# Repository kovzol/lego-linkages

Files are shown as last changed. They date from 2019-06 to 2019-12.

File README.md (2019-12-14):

# Introduction

This is a collection of simple LEGO linkages that can follow a prescribed motion.
The drawings and assembly instructions are created with the [LEGO Digital Designer (LDD)](https://www.lego.com/en-us/ldd) 4.3,
a free application for Windows and Mac. (Linux users may want to use [CrossOver](https://www.codeweavers.com/products/crossover-linux)
to run LDD with emulation.) After installing LDD, in case you have problems with the Hinge tools,
consider checking [this page](https://steamcommunity.com/sharedfiles/filedetails/?id=455735233).

The linkages are built from a minimal set of LEGO parts. The focus is on the requirement that all
linkages could be built quickly and their movement could be traced on a piece of
paper. See *author's presentation* with title [Teaching algebra and geometry with LEGO and linkages](https://www.researchgate.net/publication/332303931_Teaching_algebra_and_geometry_with_LEGO_and_linkages)
on further details on the topic. Also, an [arXiv paper](https://arxiv.org/abs/1909.04964) is available on using these
linkages in a maths camp.

In LDD one will want to set *View* > *New themes* > *LDD Extended* to make it possible to use
a much wider set of colors for each part.

## The linkages

In all models there is a long red
beam with 15 holes (actually its practicable size is just 14 units) which will be
used to firmly hold the model with the one hand (for right-handed persons this
is the left hand), and a G2 type pen refill which will be inserted in a certain connector
peg, and held and moved with the other hand, on a sheet of paper. This sheet of
paper will be pressed down by the whole construction, practically by the force
of the one hand.

In some linkages an A2 type refill should be used. It ensures a longer distance between
the sheet of paper and the beam than the G2 type, but assembling the linkage should be performed more carefully.
In such cases it may be useful to insert the refill first in the connector peg as deeply as possible,
and only then put the peg in the beam. This has to be done in some cases downside-up, in particular
in the [Parallelograms](#parallelograms). For the other ones an upside-down insertion should work.
Note that A2 type refills can provide a certain backlash in their vertical motion. Make sure you get familiar with their use
before presenting a linkage that is based on A2. Otherwise the drawings could be quite inaccurate.

Before buying the refills you need to note that some G2 type refills are longer than expected and do not ensure an accurate motion.
Some A3 type refills are sometimes sold as A2 type, so be careful when ordering a higher amount of
refills. A3 type refills can also be used but they require more careful calibration of their
vertical position, so A2 refills are always preferred. In a doubt you can try the following products:

* G2: [Kugelschreiberminen Kyome](https://www.plate.de/p/kugelschreiberminen-kyome_45244.html)
* A2: [Schneider Office 575M ISO 12757-2](https://www.myuberpens.com/new-schneider-575-75-office-black-ballpoint-pen-metal-slim-refill-iso-12757-2-a2-made-in-germany-fits-most-vintage-pens.html)

Some linkages contain one or more 1x1 beams that was recently introduced by LEGO
and may be missing from most basic sets. These parts are not absolutely required, but using
them makes the linkage more stable.

### Compass

The simplest linkage is a compass. It produces a regular circular curve.

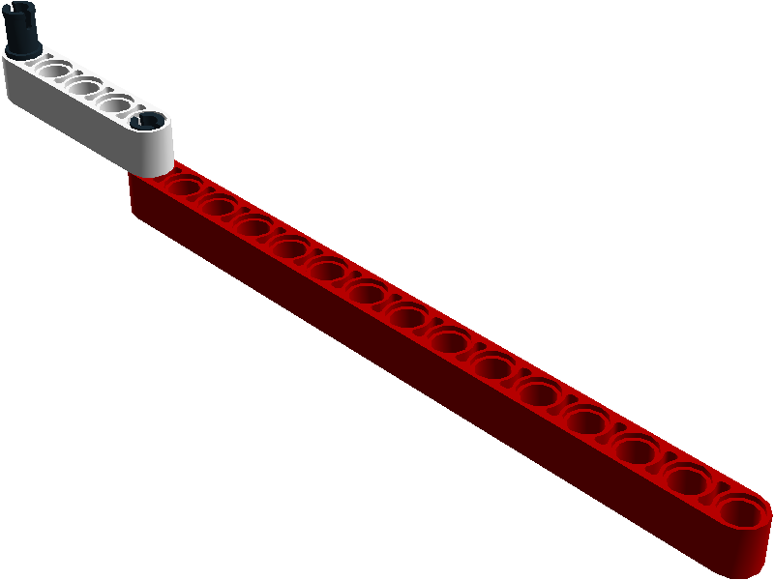
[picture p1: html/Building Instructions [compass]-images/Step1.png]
compass


[Building Instructions](http://htmlpreview.github.io/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).

### Watt's linkage

It is somewhat more difficult... a straight motion to produce. Watt's linkage is an attempt to do that,
with an almost success.

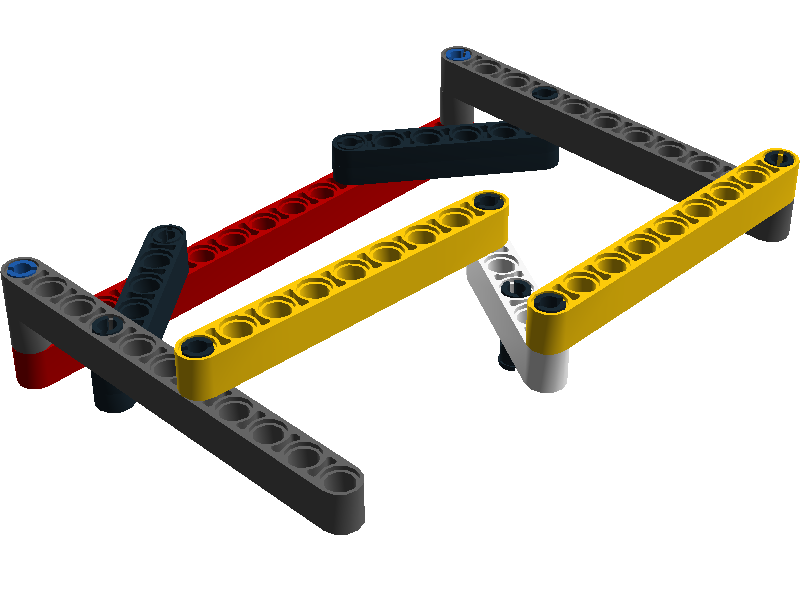
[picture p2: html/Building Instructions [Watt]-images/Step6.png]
Watt's linkage


[Building Instructions](http://htmlpreview.github.io/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).

### Parallelograms

Parallelograms can give a better understanding on the algebraic properties of the movements. Use the A2 refill to draw with them.

#### 8-5

A circle and a lemniscate will be produced, the latter occurs when the parallelogram turns into an anti-parallelogram.

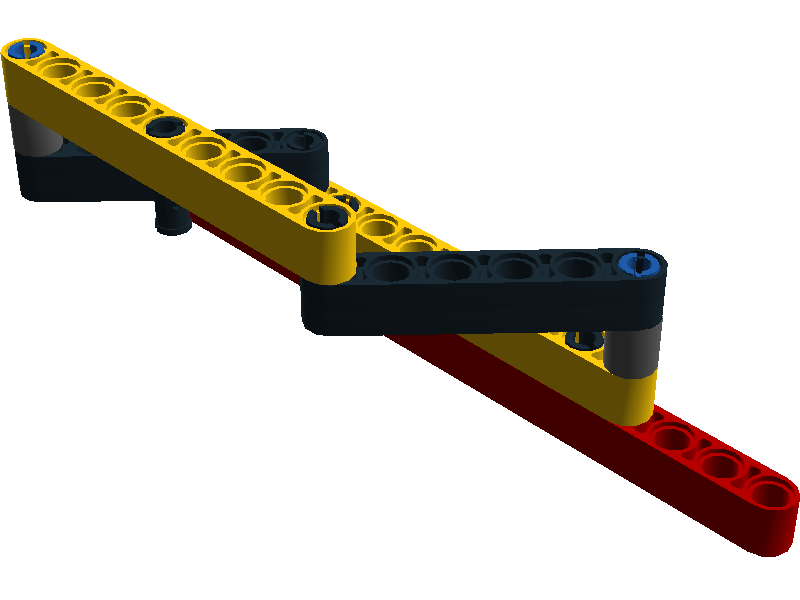
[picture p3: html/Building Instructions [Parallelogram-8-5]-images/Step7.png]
Parallelogram-8-5


[Building Instructions](http://htmlpreview.github.io/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).

#### 4-8

A circle and an almost-circle (a Cassini-oval) will be produced, the latter occurs when the parallelogram turns into an anti-parallelogram.

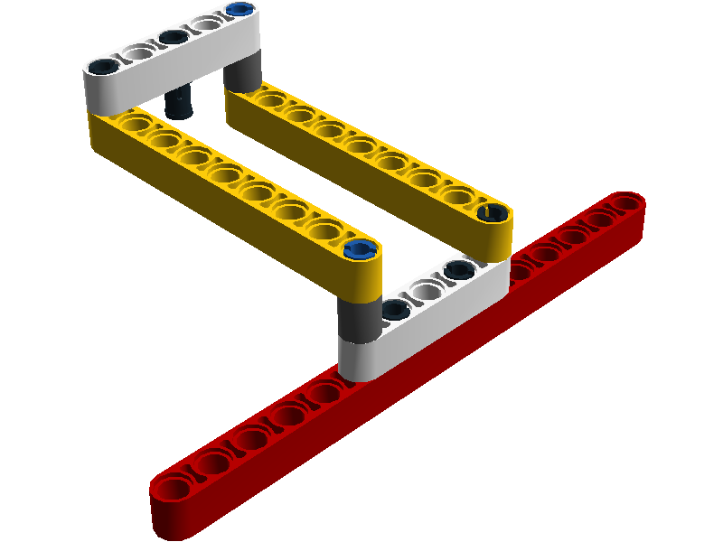
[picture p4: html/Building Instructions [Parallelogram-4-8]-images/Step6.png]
Parallelogram-4-8


[Building Instructions](http://htmlpreview.github.io/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).
This linkage will automatically turn into an anti-parallelogram when the pen refill reaches a critical point.

#### Rhombus

Three circles will be produced. This linkage is actually just a sketch, so the pen refill cannot be used to draw anything.

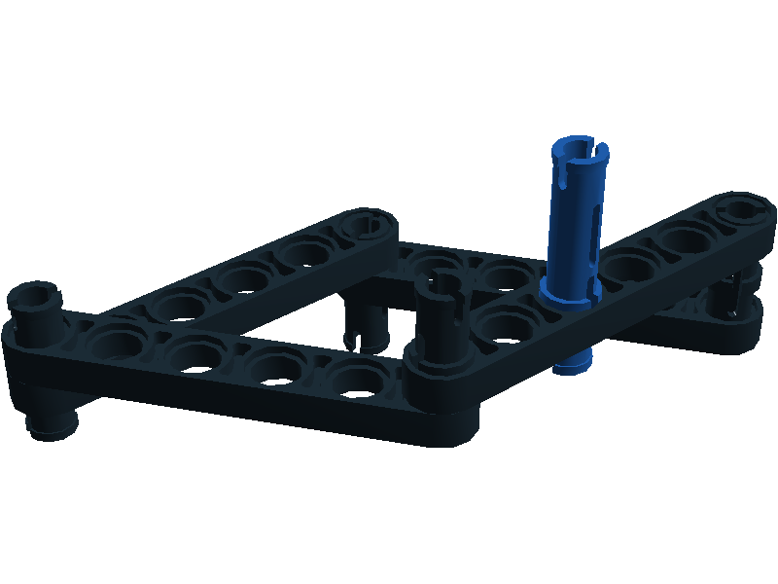
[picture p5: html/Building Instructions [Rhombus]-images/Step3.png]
Rhombus


[Building Instructions](http://htmlpreview.github.io/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).

### Chebyshev's linkage

This is a kind of generalization of the parallelograms (similarly to Watt's linkage). Use a G2 refill.

#### First approach

Chebyshev's linkage seems to produce a circular arc.

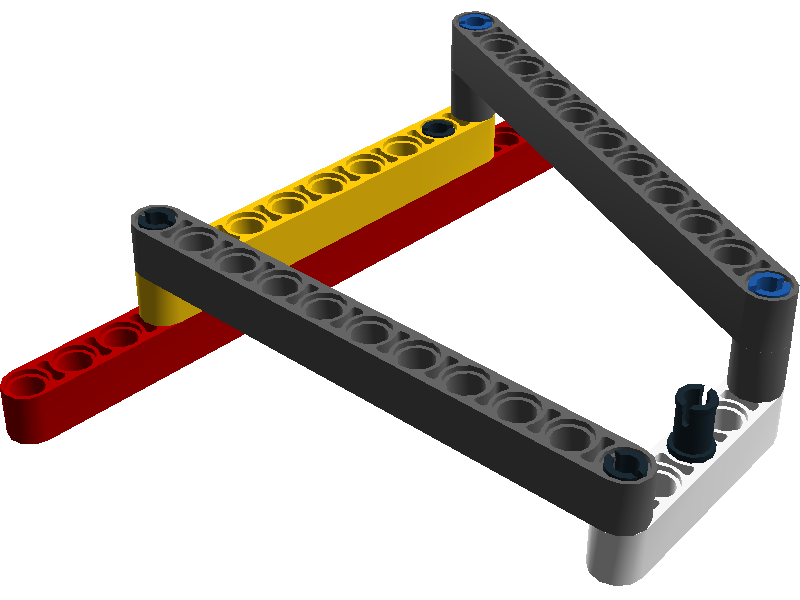
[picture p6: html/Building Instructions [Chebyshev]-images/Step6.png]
Chebyshev's linkage


[Building Instructions](http://htmlpreview.github.io/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).

When its grey bars are crossed, the linkage seems to produce a linear motion.

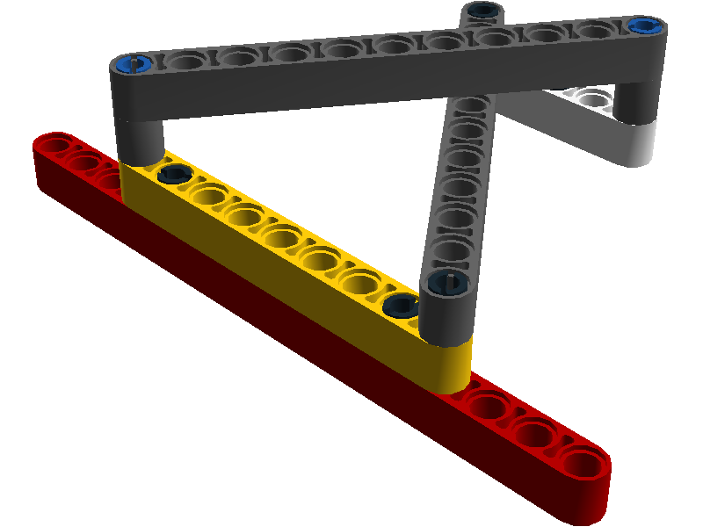
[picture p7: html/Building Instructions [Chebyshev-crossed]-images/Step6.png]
Chebyshev's linkage, crossed bars


#### Second approach

Chebyshev's lambda linkage is equivalent to the previous one, but it can create its path
in one movement as well.

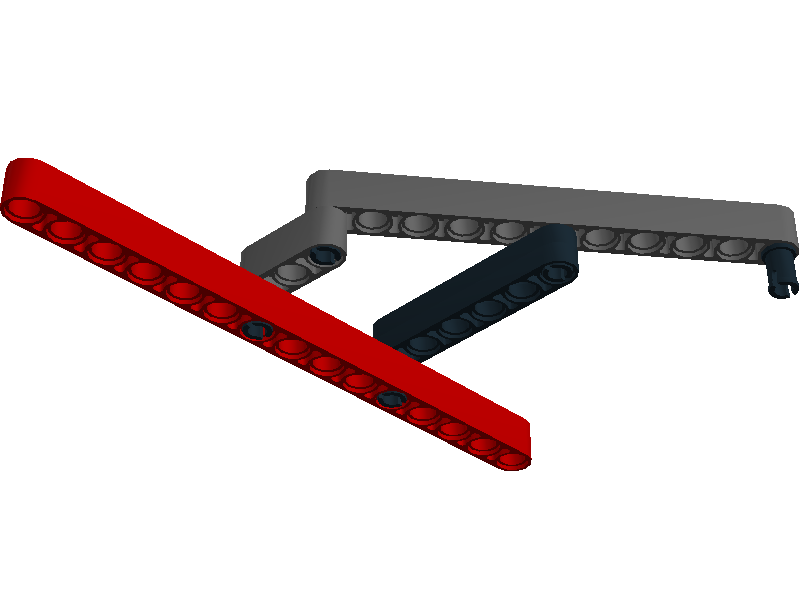
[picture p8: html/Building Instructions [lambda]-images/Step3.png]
Chebyshev's lambda linkage


[Building Instructions](http://htmlpreview.github.io/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).

### Peaucellier's linkage

#### First approach

Peaucellier's linkage provides a linear motion when putting a pen refill in the top-right position.

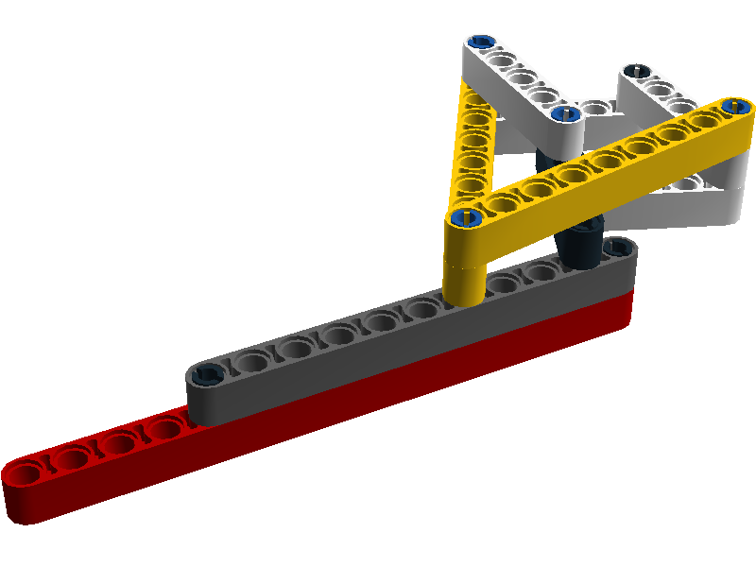
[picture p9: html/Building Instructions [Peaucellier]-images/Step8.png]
Peaucellier's linkage


See also [Building Instructions](http://htmlpreview.github.io/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).
A [GeoGebra applet](https://www.geogebra.org/m/dhpbsjdB) is also available that can be changed a little bit
to get exactly the same motion: *l<sub>1</sub>* has to be set to 8 and *l<sub>2</sub>* to 4 units. Then,
by showing the output labelled with *a* we learn that radius of the circle needs to be 3 units.

Unfortunately there exists no LEGO beam with 3 units (that is, with 4 holes), so we need to use a bigger one.
Here a 4 units long beam is used (with 5 holes). The standard kit (explained in the author's presentation
on page 93 in the Shopping list slide) has to be extended by two blue long pins, one white 5 holes beam
and one black 5 holes beam.

Alternatively a 3 units long beam with 4 holes could be printed with a 3D printer instead of the black 5 holes beam,
see [Andreas Kiener](https://www.uni-salzburg.at/index.php?id=205610)'s [contribution](3d-printing/technic-4m.openjscad.txt) as an
[OpenJSCAD](https://openjscad.org/) file.
In addition, instead of the 11-long beam two halves of 6-long beams may also be used (see a
[photo](3d-printing/Peaucellier.jpg)).

#### Second approach

If we omit a possible requirement that the ball pen point needs to intersect the line of the red beam in the same
distance as the two long beams are, then we can build a Peaucellier-type linkage with the standard set as well.
In this case we need only an extra long pin that is a minimal extra cost and no 3D printing is required.
Another benefit is that the drawn line is quite long (about 12 cm). This linkage requires an A2 type refill.

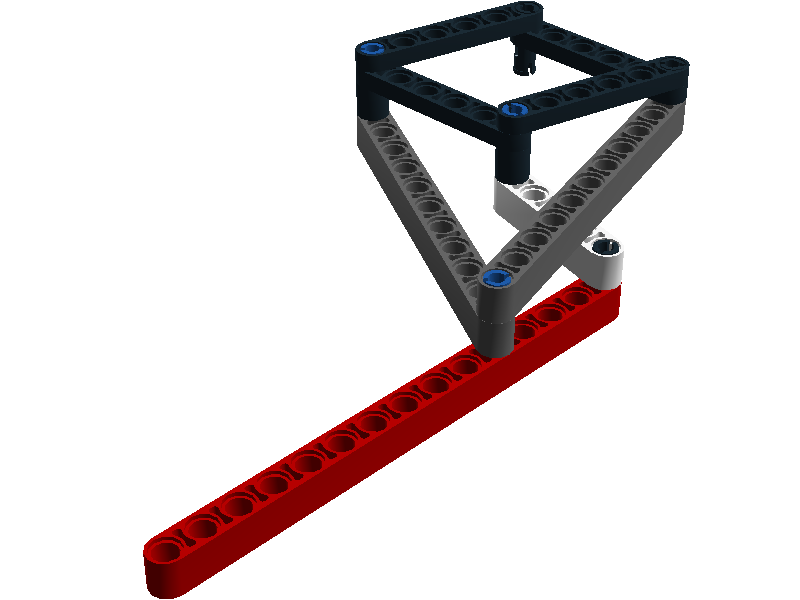
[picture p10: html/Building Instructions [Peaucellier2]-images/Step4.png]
Peaucellier's linkage, second approach


See also [Building Instructions](http://htmlpreview.github.io/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).

### Incomplete linkage as a puzzle

Students may want to solve a puzzle by completing Peaucellier's cell to complete it to the linkage that
produces a straight line. This construction is same as the previous but we just omitted the white constraint.

See the [Building Instructions](http://htmlpreview.github.io/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).

### Hart's A-frame

Another linear motion that requires an A2 pen refill. It is the same linkage that is shown in the author's
presentation on page 88 and [was announced in his blog](https://kovz0l.blogspot.com/2018/08/harts-frame-revisited.html).
There is one minor modification, however. There are two 1x1 parts used to get the linkage more fixed,
according to Andreas' idea.

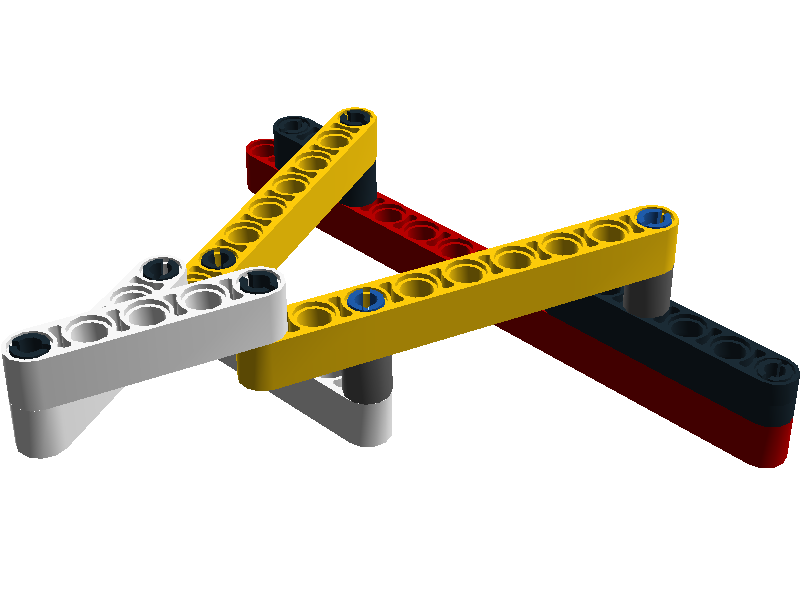
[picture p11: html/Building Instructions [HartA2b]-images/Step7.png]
Hart's A-frame


A big advantage of an earlier version of this linkage is that a much longer straight line can be drawn with it.
Another possibility is to use
the black 5 holes beam from the extended set (see Peaucellier's linkage above) instead of the two half 6 holes beam.

Here are the [Building Instructions](http://htmlpreview.github.io/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).

### Hart's inversor

Another element of the kit that produces a linear motion (again, with a G2 pen refill).

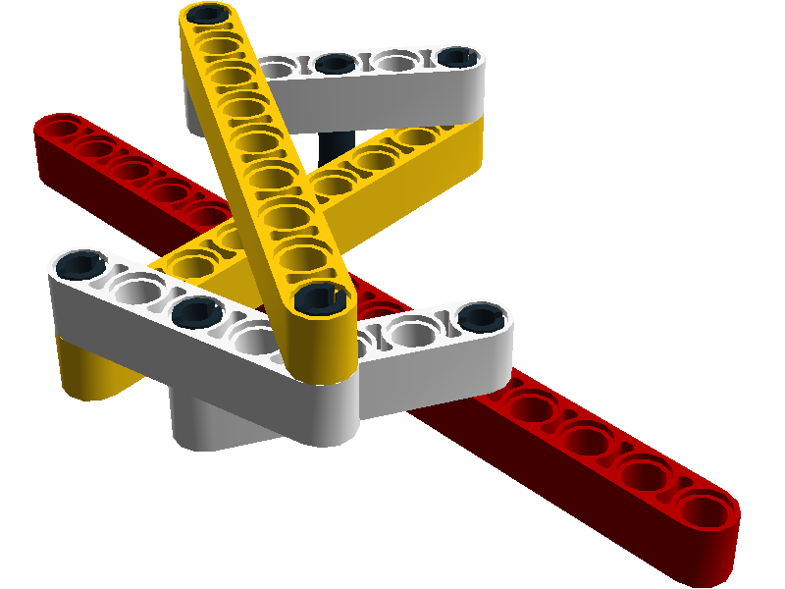
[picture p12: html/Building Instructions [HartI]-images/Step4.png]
Hart's inversor


[Building Instructions](http://htmlpreview.github.io/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).

## Suggested LEGO set to use

Author's presentation suggests the *standard set* (version 2 in the table below). To build the second approach of the Peaucellier cell, one
also needs to have another long pin. Two 1x1 parts can be very useful to minimize vertical movement of the linkage,
that is, to take up the slack. Here is an up-to-date list of the parts of the suggested LEGO set:

| Ver&shy;sion | Date | Beam 15 red 32278 | Beam 11 gray 32525 | Beam 9 yel&shy;low 40490 | Half beam 6 gray 32063 | Beam 5 white 32316 | Beam 3 gray 32523 | Beam 1x1 gray 18654 | Long pin blue 6558 | Pin black 2780 | G2 re&shy;fill | A2 re&shy;fill | 
|:---:|:---:|:---:|:---:|:---:|:---:|:---:|:---:|:---:|:---:|:---:|:---:|:---:|
| 1 | Dec 2017 | 1 | 2 | 2 | 4 | 3 | 1 | - | 2 | 9 | 1 | - |
| 2 | Feb 2019 | 1 | 2 | 2 | 4 | 3 | 1 | - | 2 | 9 | 1 | 1 |
| 3 | Jun 2019 | 1 | 2 | 2 | 4 | 3 | 1 | 2 | 3 | 9 | 1 | 1 |

## Used pen refills in the linkages
| Linkage | G2 | A2 |
|:---:|:--:|:--:|
| compass | x  | |
| Watt | x  | |
| Parallelogram-8-5 | | x  |
| Parallelogram-4-8 | | x  |
| Chebyshev | x  | |
| lambda | x  | |
| Peaucellier | x  | |
| Peaucellier2 | | x  |
| P-cell | | x  |
| HartA2b | | x  |
| HartI | x  | |

# Acknowledgements

* Tomás Recio (for the idea)
* Benedek Kovács (for constructing some of the linkages in LDD)
* Alex Mittermayr (for several ideas on the method how the linkages should be built)
* Andreas Kiener (for minor improvement ideas)
* Chris Sangwin (for several mathematical ideas and concepts from his book [How round is your circle?](https://press.princeton.edu/titles/8624.html))

Many thanks for additional support to:
* Georg Grasegger
* Markus Hohenwarter
* Barbara Lichtenegger
* M. Pilar Vélez
* Susanne Thrainer

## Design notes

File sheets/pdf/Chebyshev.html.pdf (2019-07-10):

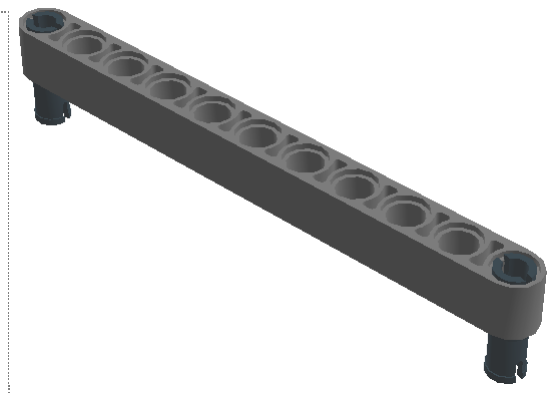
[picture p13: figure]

1 x

2 x

Step 1 of 6

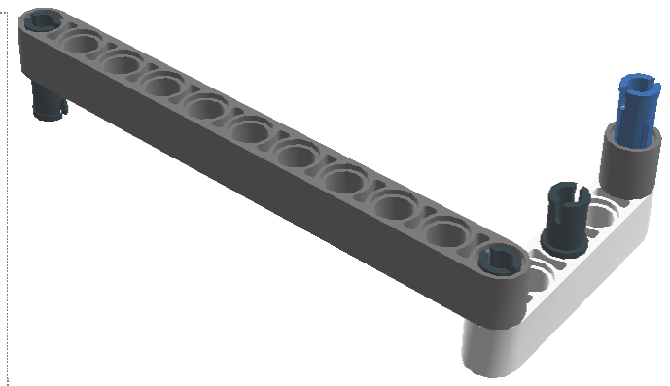
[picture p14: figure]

1 x

1 x

1 x

1 x

Step 2 of 6

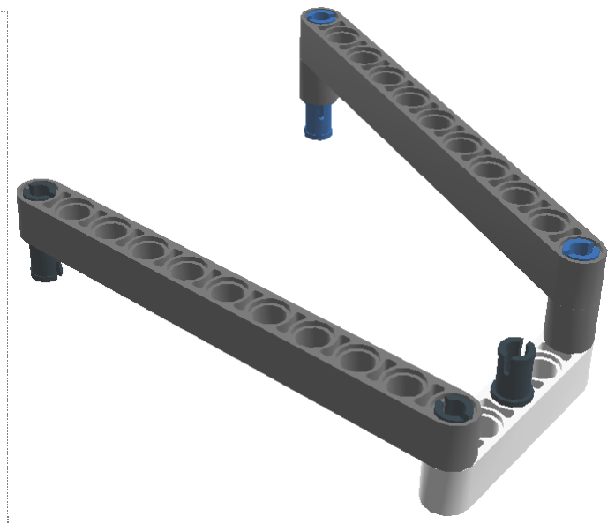
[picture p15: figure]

1 x

1 x

1 x

Step 3 of 6

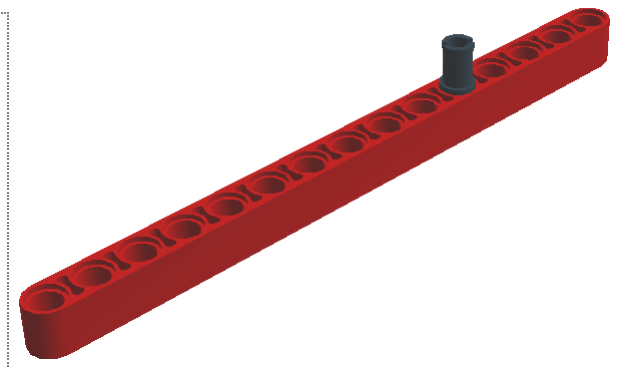
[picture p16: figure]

1 x

1 x

Step 4 of 6
Step 5 of 6

# Chebyshev

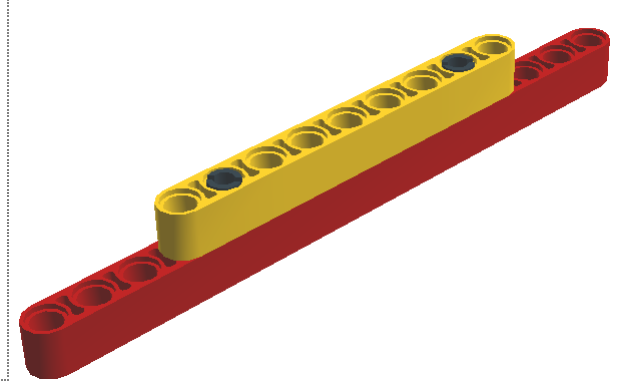
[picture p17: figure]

1 x

1 x

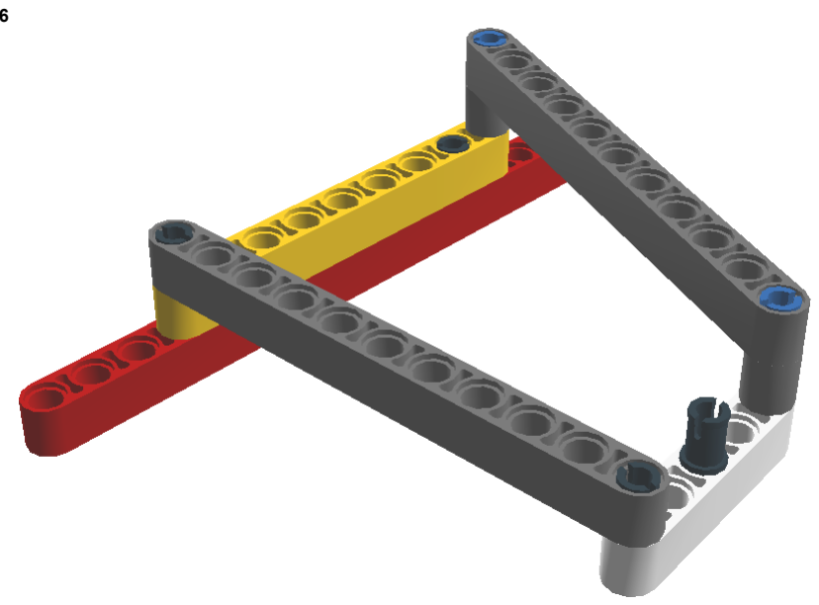
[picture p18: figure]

Step 6 of 6

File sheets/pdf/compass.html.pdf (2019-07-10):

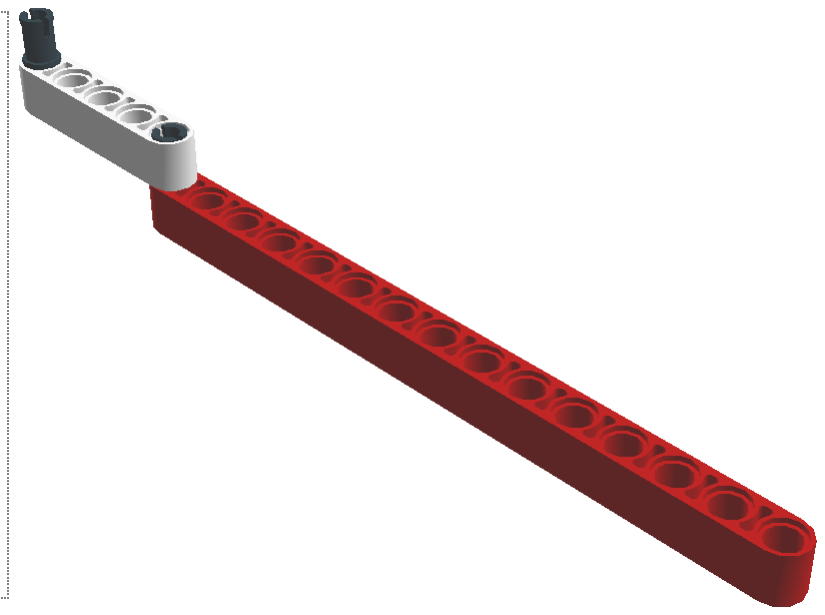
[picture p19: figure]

1 x

1 x

2 x

Step 1 of 1

# compass

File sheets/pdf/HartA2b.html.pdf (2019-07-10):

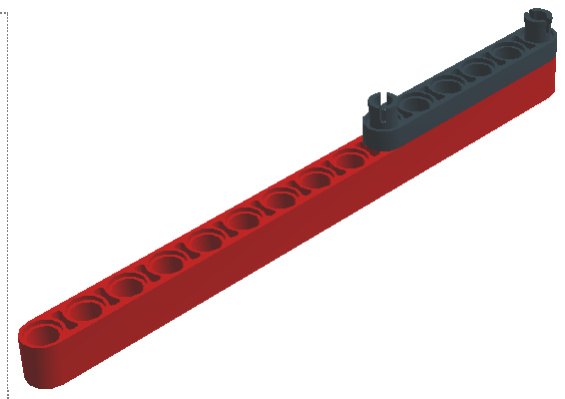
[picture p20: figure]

1 x

1 x

2 x

Step 1 of 7

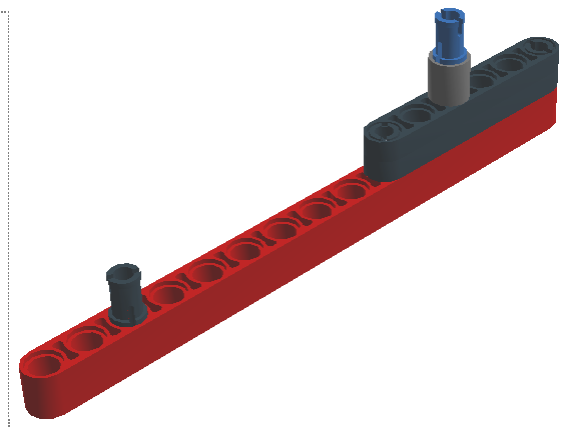
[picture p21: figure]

1 x

1 x

1 x

1 x

Step 2 of 7

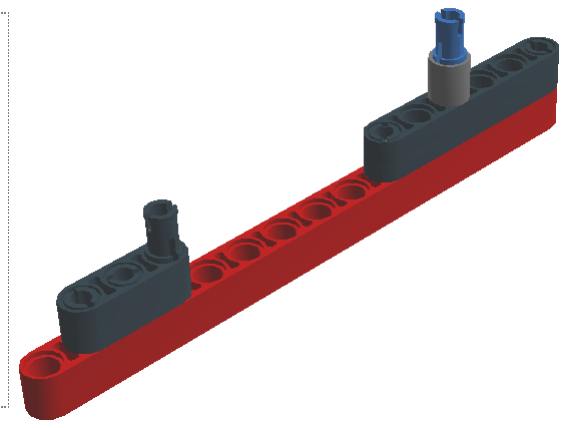
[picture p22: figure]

1 x

2 x

Step 3 of 7

1 x

1 x

Step 4 of 7

# HartA2b

1 x

1 x

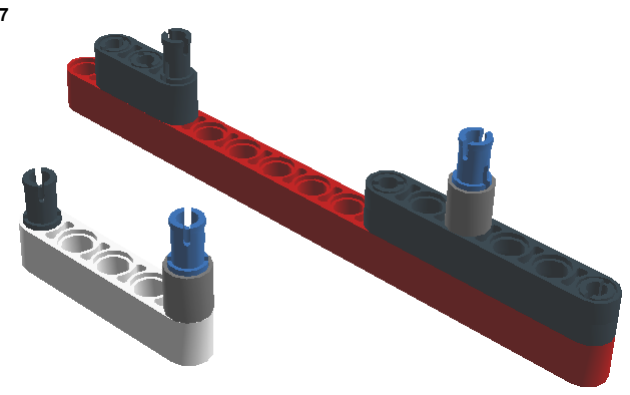
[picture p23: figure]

Step 5 of 7

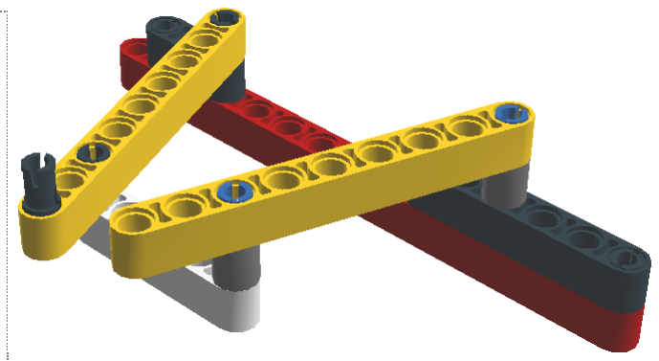
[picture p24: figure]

2 x

1 x

Step 6 of 7

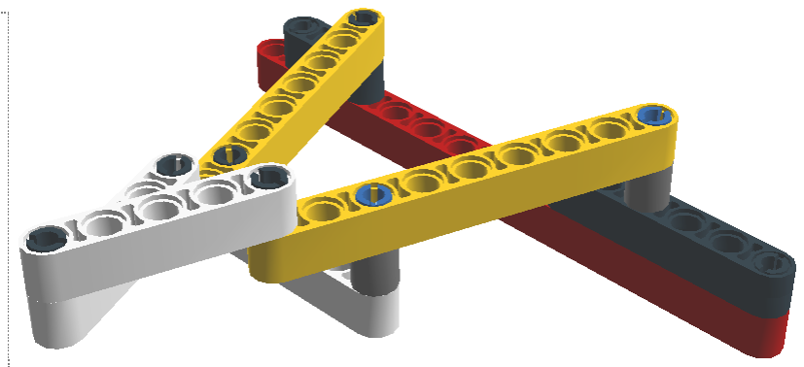
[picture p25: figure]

2 x

1 x

1 x

Step 7 of 7

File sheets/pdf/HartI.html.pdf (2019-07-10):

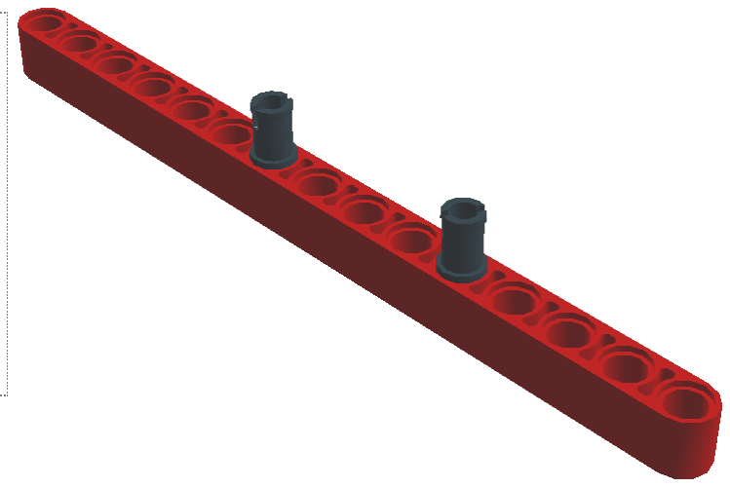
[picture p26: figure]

1 x

2 x

Step 1 of 4

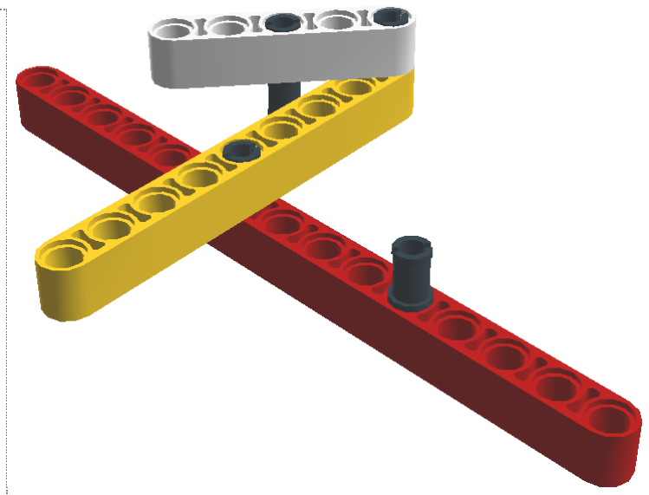
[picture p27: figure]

1 x

1 x

2 x

Step 2 of 4

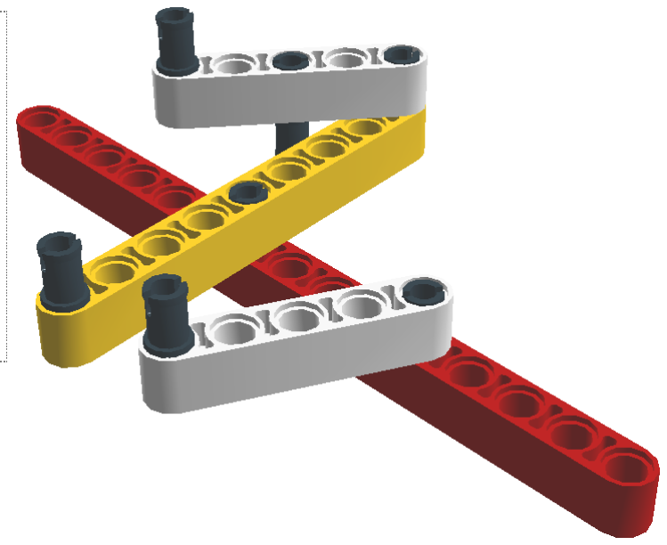
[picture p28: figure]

1 x

3 x

Step 3 of 4

1 x

1 x

1 x

Step 4 of 4

# HartI

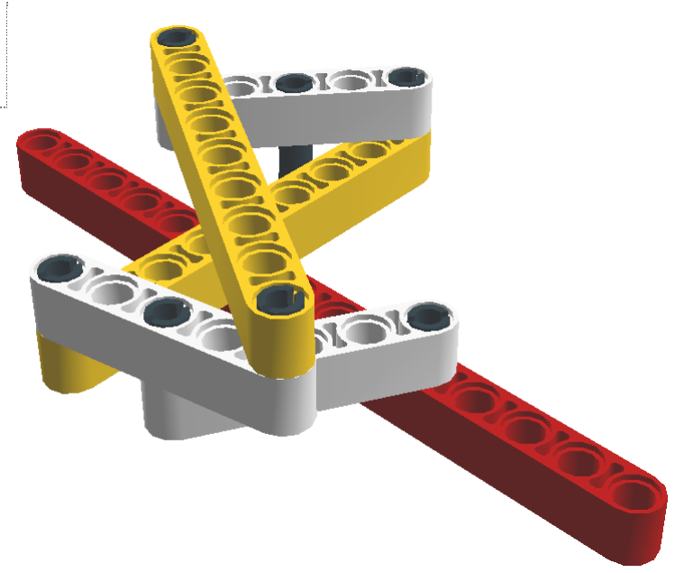
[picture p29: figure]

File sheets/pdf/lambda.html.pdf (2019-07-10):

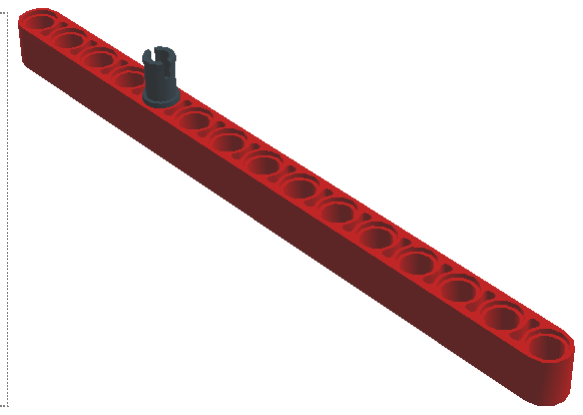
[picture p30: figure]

1 x

1 x

Step 1 of 3

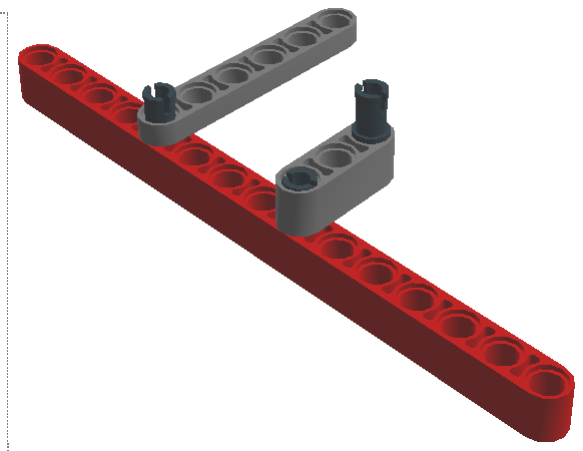
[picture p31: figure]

1 x

1 x

2 x

Step 2 of 3

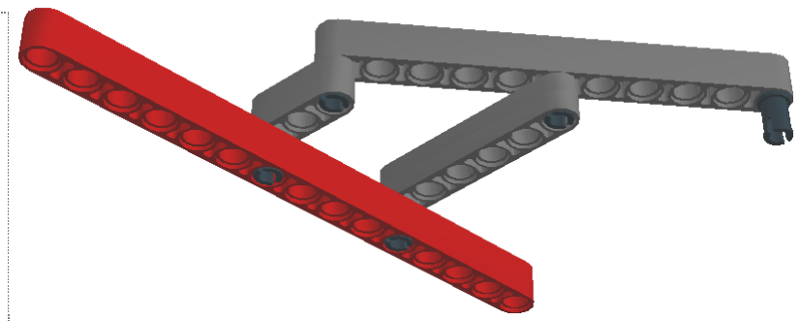
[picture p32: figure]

1 x

1 x

2 x

Step 3 of 3

# lambda

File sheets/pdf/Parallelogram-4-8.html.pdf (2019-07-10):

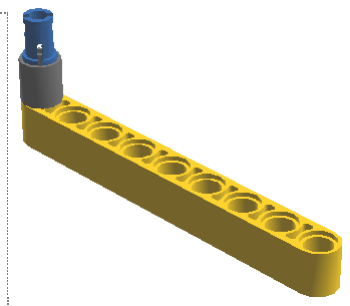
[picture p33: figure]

1 x

1 x

1 x

Step 1 of 6

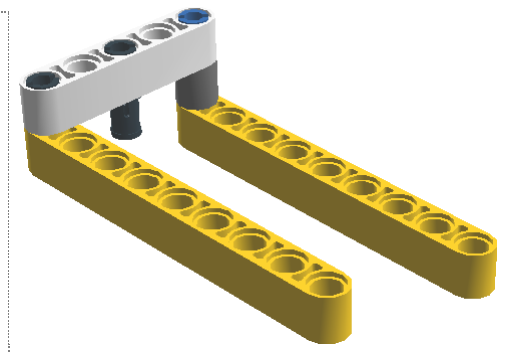
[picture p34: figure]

1 x

1 x

2 x

Step 2 of 6

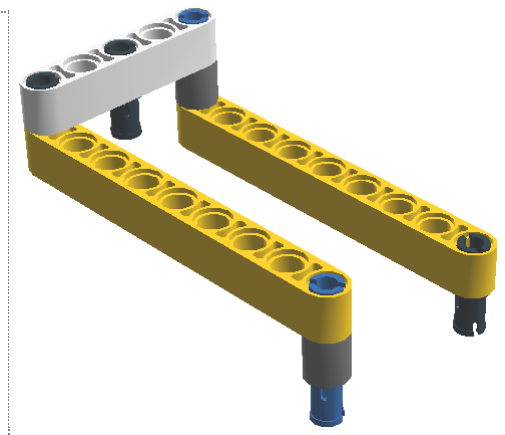
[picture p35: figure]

1 x

1 x

1 x

Step 3 of 6

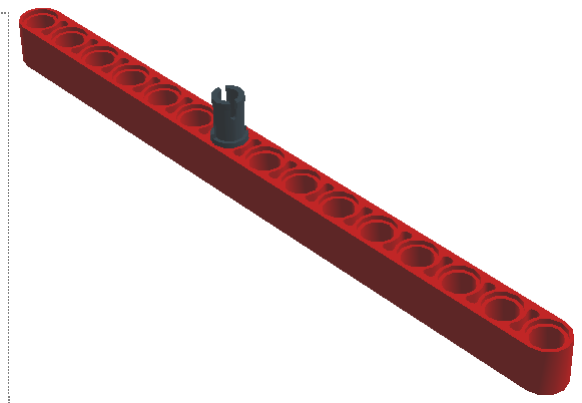
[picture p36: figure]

1 x

1 x

Step 4 of 6
Step 5 of 6

# Parallelogram-4-8


1 x

1 x


Step 6 of 6

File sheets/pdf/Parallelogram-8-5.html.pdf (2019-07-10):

1 x

Step 1 of 7

2 x

1 x

1 x

Step 2 of 7


1 x

1 x

2 x

Step 3 of 7


1 x

1 x

1 x

Step 4 of 7

1 x

Step 5 of 7

# Parallelogram-8-5


2 x


1 x

Step 6 of 7


Step 7 of 7

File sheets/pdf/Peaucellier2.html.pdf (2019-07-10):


1 x

1 x

1 x

1 x

Step 1 of 4


1 x

1 x

1 x

1 x

Step 2 of 4


1 x

1 x

1 x

1 x

Step 3 of 4

# Peaucellier2


3 x

1 x

Step 4 of 4

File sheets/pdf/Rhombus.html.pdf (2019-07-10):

1 x

Step 1 of 3


2 x

2 x

Step 2 of 3


1 x

2 x

1 x

Step 3 of 3

# Rhombus

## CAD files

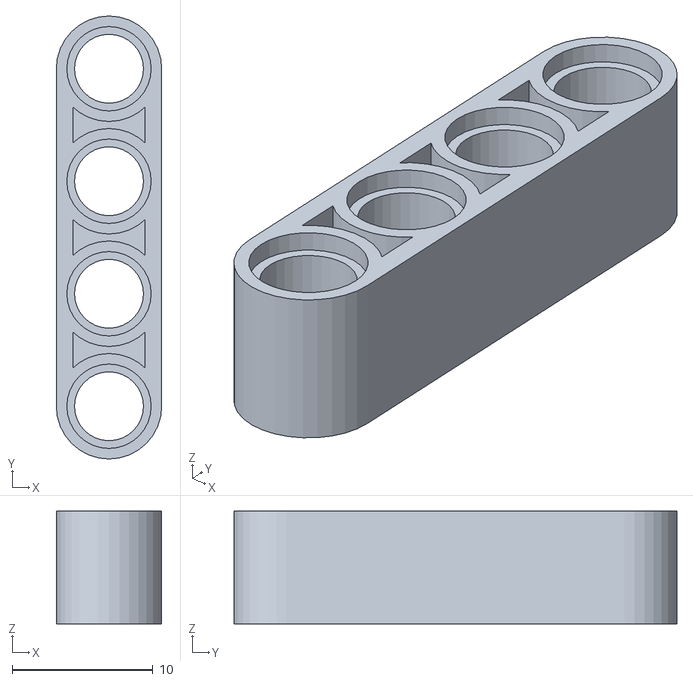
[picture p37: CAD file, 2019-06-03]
3d-printing/technic-4m.stl
7.50 x 31.5 x 8.00

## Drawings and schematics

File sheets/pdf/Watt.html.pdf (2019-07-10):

# Watt

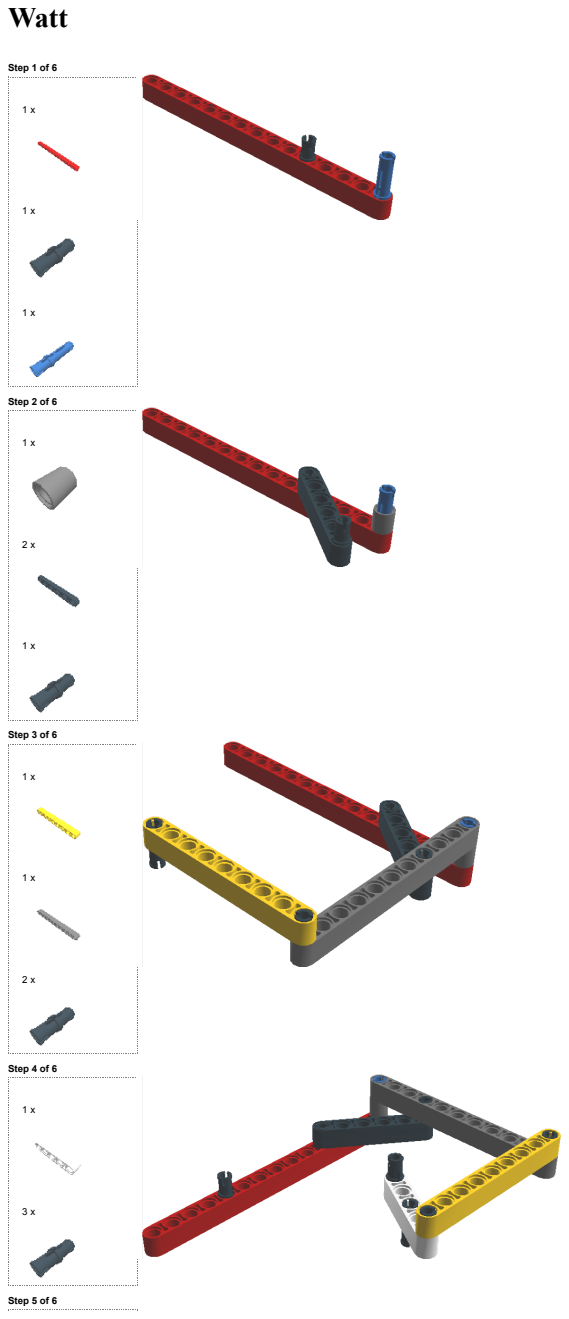
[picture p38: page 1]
Step 1 of 6; Step 2 of 6; Step 3 of 6; Step 4 of 6; Step 5 of 6

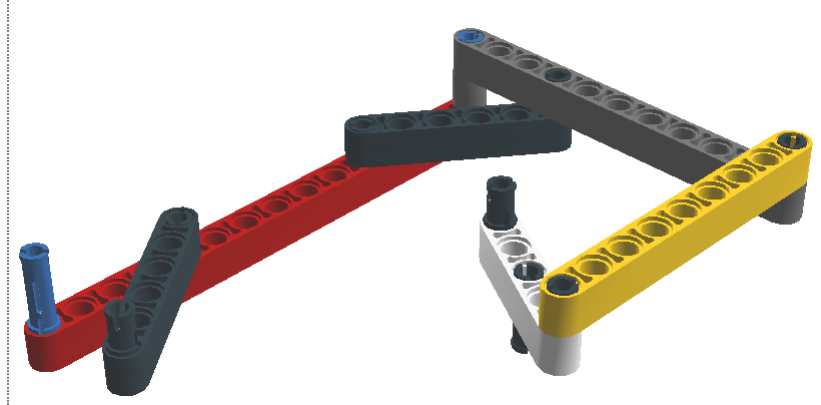
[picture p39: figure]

2 x

1 x

1 x

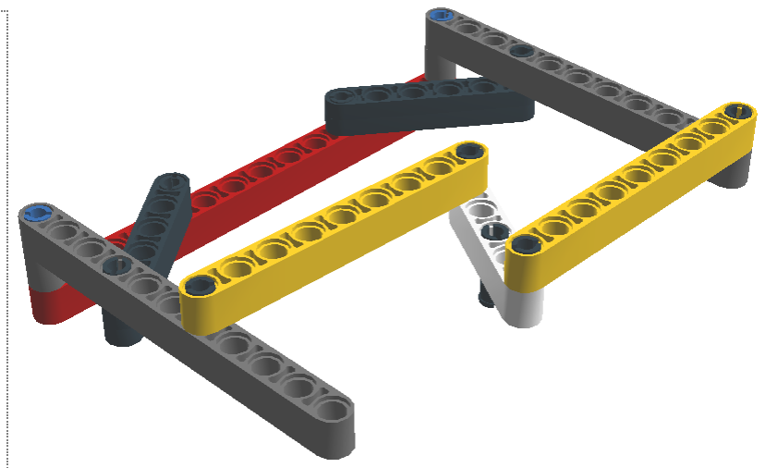
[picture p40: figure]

1 x

1 x

1 x

1 x

Step 6 of 6

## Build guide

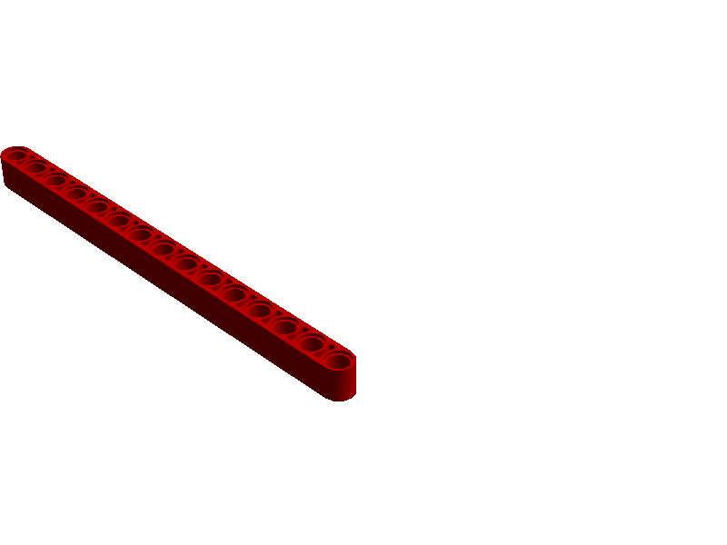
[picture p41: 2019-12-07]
html/Building Instructions [P-cell]-images/Step1.png

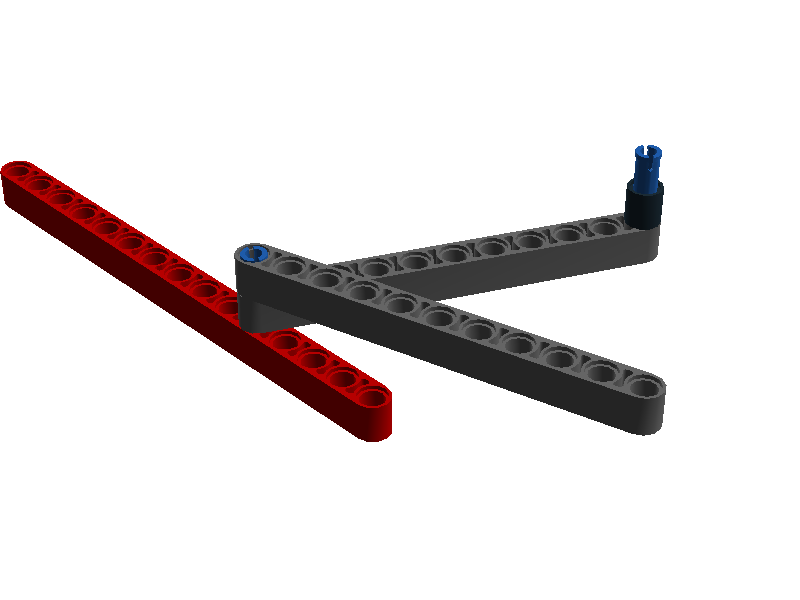
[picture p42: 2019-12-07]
html/Building Instructions [P-cell]-images/Step3.png

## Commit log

2019-06-03 Add Hart's A-frame
2019-06-03 Add OpenJSCAD files
    [technic-4m.stl]
2019-06-03 Add hint on problem with Hinge tools
2019-07-10 Add two scripts to create building instructions in a printable format
